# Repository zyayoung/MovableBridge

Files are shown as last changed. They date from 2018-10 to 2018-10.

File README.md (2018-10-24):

# MovableBridge

## Introduction

### Circuit Diagram

Our bridge must know whether there is a car A or B on it and whether there is a big car (ship) is waiting below or passing. To fulfill this requirement, we need two infrared object sensor to judge whether there is a car on the bridge and two ultrasonic distance sensors to detect whether is a ship waiting/passing under the bridge.

Next, we must raise the bridge when there is a ship waiting under the bridge and there is no car on the bridge. To fulfill this requirement, we need two DC motors and a DC motor driver.

Then, we need to stop the car when the bridge is going to raise or have been raised, so we need a servo (to raise and lower the blocking system) and two LEDs (red and green) each side.

Furthermore, we need an Arduino to read the sensors and control the bridge-raising system and the car-blocking system.

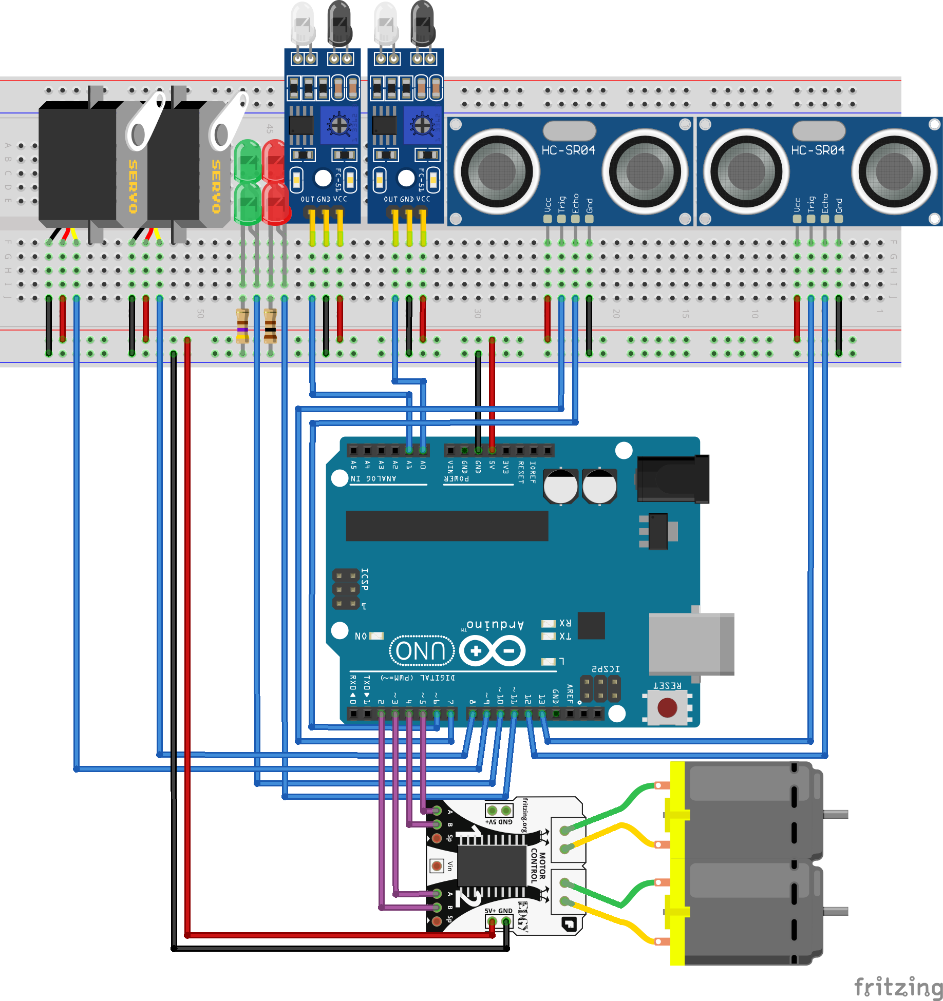
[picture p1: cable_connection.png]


In the circuit diagram, we label all 5v by red and GND by black. Since a single N20 motor only need 0.3W@6v when raising the bridge and 5w when being locked. Thus a power bank, which can offer 2A@5V, is enough.

### Programming

The main logic is that we keep the bridge lowered unless there is a ship waiting below and there is no car on the bridge.

We designed the program to be an automaton: it saves some states (flags) and update these states due to the readings from the sensors and take action due to the states. The main loop will be executed 10 times per second and will not be blocked unless the bridge is raising or lowering. By doing so, we can deal with unprecise readings from the ultrasonic sensors and behave correctly regardless of the sequence of testing.

For example, we use an "ultrasonic sensor current state" to indicate whether the ultrasonic sensor has detected a ship.

To update this state, we use another state to indicate the time the indication from the ultrasonic sensor remains the same. When it remains for 1s, the "ultrasonic sensor current state" will be updated.

To use this state, if the state is true (which means that there is a ship waiting below) and there is no car on the bridge (which is another state), then the bridge will be raised.

### Cable Connection

In out project, we use varnished wire.

1. Solder all 5v and GND together
2. Cut Dupont lines and extent it with varnished wire (remember to remove varnish before connecting)
3. Connect other cables

## Group members

- Dong Yulong
- Li Yixuan
- Shi Xiaotian
- Zhang Yuang

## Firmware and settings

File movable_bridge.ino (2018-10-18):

#include <Servo.h>
#define DEBUG_LEVEL 2

#define OFF_BRIDGE 0
#define ENTER_FROM_LEFT 1
#define ENTER_FROM_RIGHT 2
#define LEAVING_LEFT 3
#define LEAVING_RIGHT 4

#define SERVO_LEFT 9
#define SERVO_RIGHT 8
#define DISTANCE_LEFT A0
#define DISTANCE_RIGHT A1
#define HC_TRIG 7
#define HC_ECHO 6
#define HCMINOR_TRIG 13
#define HCMINOR_ECHO 12
#define MOTOR_LEFT_A 5
#define MOTOR_RIGHT_A 3
#define MOTOR_LEFT_B 4
#define MOTOR_RIGHT_B 2
#define SWITCH_LEFT A3
#define SWITCH_RIGHT A2
#define LIGHT_RED 11
#define LIGHT_GREEN 10

#define BLOCK_ON_DEGREE 145
#define BLOCK_OFF_DEGREE 45
#define CARC_DISTANCE_MIN 15
#define CARC_DISTANCE_MAX 50

#define DELAY_PER_LOOP 101


Servo s_left;
Servo s_right;

int carA_on_bridge = OFF_BRIDGE;
int carA_is_waiting_left = 0;
int carA_is_waiting_right = 0;
unsigned long carA_off_bridge_timer = 2001;
unsigned long carC_off_bridge_timer = 2001;
int carC_is_waiting = 0;

unsigned long distance_left_trigger_timer = 0;
unsigned long distance_right_trigger_timer = 0;
unsigned long hc_state_changed_timer = 0;
int hc_current_state = 0;

int bridge_raised = 0;

long microsecondsToCentimeters(long microseconds) {
  // cite: https://www.arduino.cc/en/Tutorial/Ping?from=Tutorial.UltrasoundSensor

  // The speed of sound is 340 m/s or 29 microseconds per centimeter.
  // The ping travels out and back, so to find the distance of the object we
  // take half of the distance travelled.

  return microseconds / 29 / 2;
}


long hc_read() {
  // cite: https://www.arduino.cc/en/Tutorial/Ping?from=Tutorial.UltrasoundSensor

  // This function return the distance read from ultrasonic senser in cm.

  long duration, cm;

  // The PING))) is triggered by a HIGH pulse of 2 or more microseconds.
  // Give a short LOW pulse beforehand to ensure a clean HIGH pulse:
  digitalWrite(HC_TRIG, LOW);
  delayMicroseconds(2);
  digitalWrite(HC_TRIG, HIGH);
  delayMicroseconds(5);
  digitalWrite(HC_TRIG, LOW);

  // The same pin is used to read the signal from the PING))): a HIGH pulse
  // whose duration is the time (in microseconds) from the sending of the ping
  // to the reception of its echo off of an object.
  duration = pulseIn(HC_ECHO, HIGH, 8000);

  // convert the time into a distance
  cm = microsecondsToCentimeters(duration);
  return cm+10;
}

long hcminor_read() {
  long duration, cm;
  digitalWrite(HCMINOR_TRIG, LOW);
  delayMicroseconds(2);
  digitalWrite(HCMINOR_TRIG, HIGH);
  delayMicroseconds(5);
  digitalWrite(HCMINOR_TRIG, LOW);
  duration = pulseIn(HCMINOR_ECHO, HIGH, 8000);
  cm = microsecondsToCentimeters(duration);
  return cm;
}

bool detected_carc() {
  long distance = hc_read();
  delay(35);
  
  long distanceminor = hcminor_read();
  
  #if DEBUG_LEVEL == 2
  Serial.print(distance);
  Serial.print(" ");
  Serial.println(distanceminor);
  #endif
  return (CARC_DISTANCE_MIN < distance && distance < CARC_DISTANCE_MAX) || (CARC_DISTANCE_MIN < distanceminor && distanceminor < CARC_DISTANCE_MAX);
}


void setup() {
  // initialize serial communication:

#if DEBUG_LEVEL
  Serial.begin(115200);
#endif

  s_left.attach(SERVO_LEFT);
  s_right.attach(SERVO_RIGHT);
  pinMode(SERVO_RIGHT, OUTPUT);
  pinMode(HC_TRIG, OUTPUT);
  pinMode(HCMINOR_TRIG, OUTPUT);
  pinMode(MOTOR_LEFT_A, OUTPUT);
  pinMode(MOTOR_RIGHT_A, OUTPUT);
  pinMode(MOTOR_LEFT_B, OUTPUT);
  pinMode(MOTOR_RIGHT_B, OUTPUT);
  pinMode(LIGHT_RED, OUTPUT);
  pinMode(LIGHT_GREEN, OUTPUT);
  pinMode(DISTANCE_LEFT, INPUT);
  pinMode(DISTANCE_RIGHT, INPUT);
  pinMode(SWITCH_LEFT, INPUT);
  pinMode(SWITCH_RIGHT, INPUT);
  pinMode(HC_ECHO, INPUT);
  pinMode(HCMINOR_ECHO, INPUT);

  digitalWrite(MOTOR_LEFT_A, LOW);
  digitalWrite(MOTOR_LEFT_B, LOW);
  digitalWrite(MOTOR_RIGHT_A, LOW);
  digitalWrite(MOTOR_RIGHT_B, LOW);
}


void loop() {
  // Update flags

  // Update sensor trigger time for robustness
  if (!digitalRead(DISTANCE_LEFT))distance_left_trigger_timer += DELAY_PER_LOOP;
  else distance_left_trigger_timer = 0;
  if (!digitalRead(DISTANCE_RIGHT))distance_right_trigger_timer += DELAY_PER_LOOP;
  else distance_right_trigger_timer = 0;
  if (detected_carc() ^ hc_current_state)hc_state_changed_timer += DELAY_PER_LOOP;
  else hc_state_changed_timer = 0;

  // Make accurate states of the sensors
  carA_is_waiting_left = (distance_left_trigger_timer >= 250) ? 1 : 0;
  carA_is_waiting_right = (distance_right_trigger_timer >= 250) ? 1 : 0;
  if (hc_state_changed_timer > 1000) {
    hc_current_state = ! hc_current_state;
  }
  carC_is_waiting = hc_current_state;

  // Predict whether carA is on the bridge
  if (carA_on_bridge == ENTER_FROM_LEFT && carA_is_waiting_right)carA_on_bridge = LEAVING_RIGHT;
  else if (carA_on_bridge == ENTER_FROM_RIGHT && carA_is_waiting_left)carA_on_bridge = LEAVING_LEFT;
  else if (carA_on_bridge == LEAVING_LEFT && !carA_is_waiting_left) {
    carA_on_bridge = OFF_BRIDGE;
    delay(2000);  // easy but not elegant
  }
  else if (carA_on_bridge == LEAVING_RIGHT && !carA_is_waiting_right) {
    carA_on_bridge = OFF_BRIDGE;
    delay(2000);  // easy but not elegant
  }
  else if (carA_on_bridge == OFF_BRIDGE && carA_is_waiting_left && carA_off_bridge_timer > 5000)carA_on_bridge = ENTER_FROM_LEFT;
  else if (carA_on_bridge == OFF_BRIDGE && carA_is_waiting_right && carA_off_bridge_timer > 5000)carA_on_bridge = ENTER_FROM_RIGHT;

  // Update off bridge timer
  carA_off_bridge_timer = (carA_on_bridge) ? 0 : carA_off_bridge_timer + DELAY_PER_LOOP;
  carC_off_bridge_timer = (carC_is_waiting) ? 0 : carC_off_bridge_timer + DELAY_PER_LOOP;


  // Take action

  // Update Traffic Light
  bool redlight = bridge_raised || carC_off_bridge_timer < 2000;
  digitalWrite(LIGHT_RED, redlight);
  digitalWrite(LIGHT_GREEN, !redlight);

  // Update Blocking System
  s_left.write((!carA_is_waiting_left && redlight) ? BLOCK_ON_DEGREE-18 : BLOCK_OFF_DEGREE-18);
  s_right.write((!carA_is_waiting_right && redlight) ? BLOCK_ON_DEGREE-5 : BLOCK_OFF_DEGREE-5);

  // Main Operation: Raise or Lower the bridge
  // Notice that we block the loop here to prevent some strange errors
  if (!bridge_raised && carC_is_waiting && carA_off_bridge_timer > 2000) {
    // Raise the bridge ( pray that compiler can optimize the code below

#if DEBUG_LEVEL
    Serial.println("Raiseing the bridge.");
#endif

    // Switch is not used here because we are lazy.

    digitalWrite(MOTOR_LEFT_B, 1);
    digitalWrite(MOTOR_RIGHT_B, 1);
    delay(5380);
    digitalWrite(MOTOR_RIGHT_B, 0);
    delay(20);
    digitalWrite(MOTOR_LEFT_B, 0);
    bridge_raised = 1;
  }

  if (bridge_raised && carC_off_bridge_timer > 2000) {
    // Lower the bridge

#if DEBUG_LEVEL
    Serial.println("Lowering the bridge.");
#endif

    digitalWrite(MOTOR_LEFT_A, 1);
    digitalWrite(MOTOR_RIGHT_A, 1);
    delay(4730);
    digitalWrite(MOTOR_RIGHT_A, 0);
    delay(20);
    digitalWrite(MOTOR_LEFT_A, 0);
    bridge_raised = 0;
  }


  // Debug
#if DEBUG_LEVEL
  char str[100];
  sprintf(
    str,
    "carA\t|on:%d\t|wl:%d\t|wr:%d\t|t:%lu\t|carC\t|on:%d\t|t:%lu\t|bridgeraised:%d",
    carA_on_bridge,
    carA_is_waiting_left,
    carA_is_waiting_right,
    carA_off_bridge_timer,
    carC_is_waiting,
    carC_off_bridge_timer,
    bridge_raised
  );
  Serial.println(str);
#endif

#if DEBUG_LEVEL == 2
  sprintf(
    str,
    "distance_left_timer:%lu\t|distance_right_timer:%lu\t|hc_state_changed_timer:%lu",
    distance_left_trigger_timer,
    distance_right_trigger_timer,
    hc_state_changed_timer
  );
  Serial.println(str);
#endif


  // loop 1000/DELAY_PER_LOOP times per second
  delay(DELAY_PER_LOOP-25);  // minus 25 to cancel the delay in detecing the big car C
}
